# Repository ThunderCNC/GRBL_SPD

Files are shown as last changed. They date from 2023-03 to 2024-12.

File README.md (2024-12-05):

  

  <div align="center">
    <div style="display:inline-block; vertical-align: middle;">
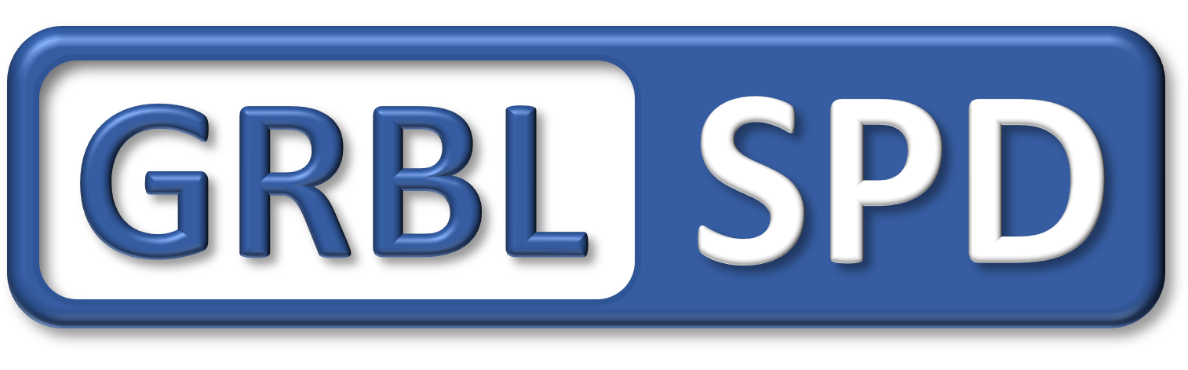
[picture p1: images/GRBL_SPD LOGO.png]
      
    </div>
  </div> 

  <div align="center" >
  <a href="https://www.ebay.ca/itm/226146198705" style="margin-right:10px">
    
  </a>
  <a href="https://www.facebook.com/ThunderCNC" style="margin-right:10px">
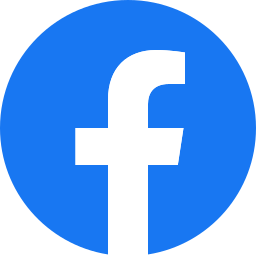
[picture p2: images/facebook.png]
Facebook
    
  </a>
  <a href="http://www.youtube.com/@Thunder116fd" style="margin-right:10px">
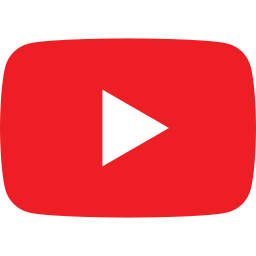
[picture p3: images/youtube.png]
Youtube
    
  </a>
  <a href="https://www.instagram.com/thunder_cnc/" style="margin-right:10px">
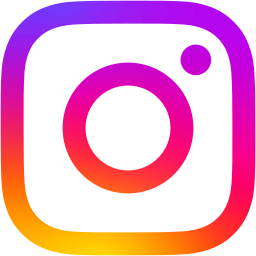
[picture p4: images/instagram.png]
Instagram
    
  </a>
  <a href="https://www.linkedin.com/in/jon-harrison-01428557" style="margin-right:10px">
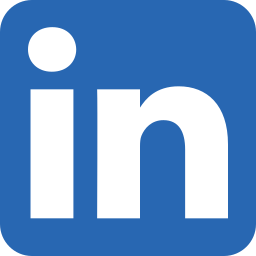
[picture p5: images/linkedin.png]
Linkedin
    
  </a>
  <a href="https://www.tindie.com/stores/gingertesla/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">
    
  </a>
  </div>
  </br>
  </br>
  <p align="center" >Developed to integrate software control of the Makita 701C for use with but not limited to the Arduino Uno board (Flashed with GRBL 1.1)
  </p>
  <h2>ABOUT THE GRBL_SPD</h2>
  <p>
    This project allows for automatic control of a standard Makita 701C router for CNC machines. GRBL_SPD lets you set the rpm for your bits in software such as Vectric and have it automatically set your router. This cicuit replaces the potentiometer in the router and has an accuracy of approximately between +/- 100 to 200 RPM. In most cases this deviation has no impact on the machining process. You no longer have to turn on the router before sending the file, GRBL_SPD will do it for you. There are inputs for manual control which overrides the RPM setting in the GRBL file being sent. 
  </p></br>
  <h2>VERSIONS</h2>
  <div>
    <h2>Version 3 -- Discontinued</h2>
    <p> Reason: ATtiny84 microcontroller reached end of life.</p>
    <a title="Go to v3 page" href="versions/Version_3.md">
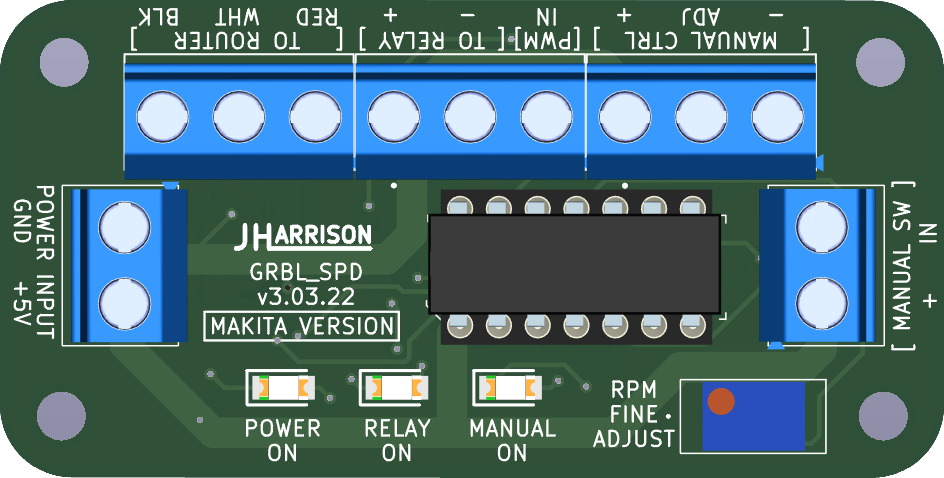
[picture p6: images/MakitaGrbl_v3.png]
      
    </a>
  </div></br>
  <div>
    <h2>Version 4 -- Available</h2>
    <p> Upgraded to ATtiny1624 microcontroller</p>
    <a title="Go to v4 page" href="versions/Version_4.md">
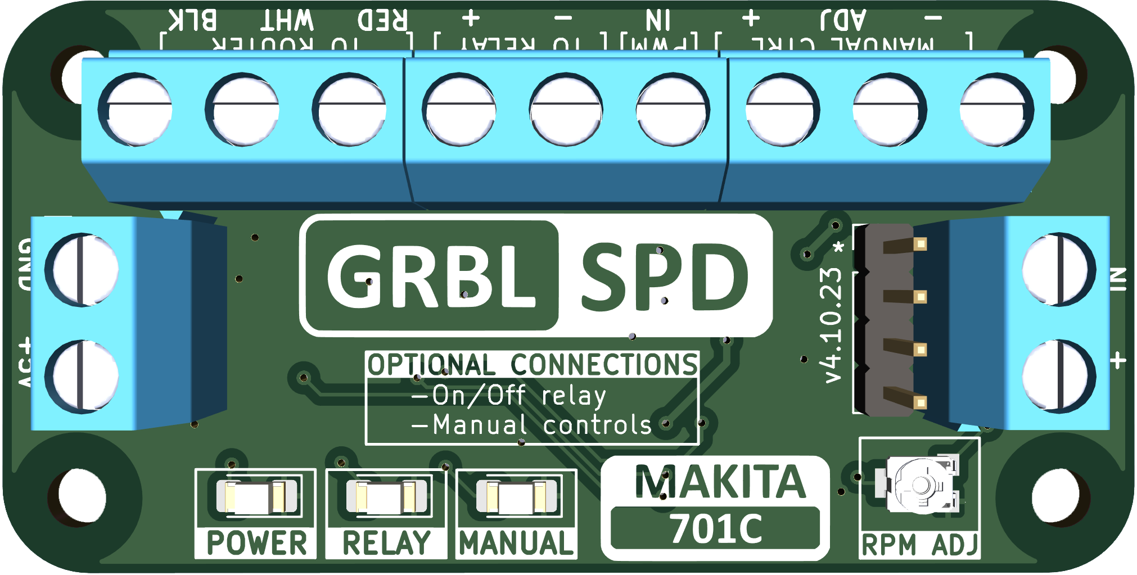
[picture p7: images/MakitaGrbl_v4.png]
      
    </a>
  </div></br>
  <!--<div>
    <h4>Version 5 -- Coming Soon</h4>
    <a title="Go to v5 page" href="versions/Version_5.md">
      <img height="150" src="images/MakitaGrbl_v5.png">
    </a>
  </div></br> -->

  <p> 
    <h2>Version 4 Features:</h2>
    <ul>
      <li>20MHz ATtiny1624 microcontroller</li>
      <li>10,000 to 30,000 RPM</li>
      <li>On/Off relay control</li>
      <li>Auto off when using manual override</li>
      <li>External manual controls</li>
    </ul>
  </p>

  <h2>Prerequisites:</h2>
    <ul>
      <li>+5v power and ground from CNC controller</li>
      <li>0-5v PWM signal from CNC controller</li>
      <li>1kHz PWM signal</li>
      <li>Sheilded cable between router and GRBL_SPD</li>
    </ul>

  <h2>Optional:</h2>
    <ul>
      <li>Connect relay for on/off function</li>
      <li>Potentiometer and switch for manual controls</li>
    </ul>

  <h3>Videos:</h3>
    <ul>
      <li>https://youtu.be/yv5z3KrGrSQ</li>
      <li>https://youtu.be/ecWwXNGC7Bc</li>
    </ul>

  <h4>Some users have tested with 240v Makita versions and have it functioning. I am not able to confirm this other than some video and testimony from those users. This board is designed for the Makita 701C so any other models will be experimenting at your own risk.</h4>

  Links to videos from Derek using the Makita 700C 240vac.
    <ul>
      <li>https://youtu.be/zJGl1yo-icU</li>
      <li>https://youtu.be/4u-4MBUV964</li>
    </ul>
  
  <h3><STRONG>WARNING!</STRONG> Voltages above 5v connected to this board will damage the microcontroller. If experimenting with controllers other than the standard Uno be sure to double check voltages and/or add protection to inputs. Zener and resistor for example.</h3>
  <h3>Possible high voltage setup:</h3>
  <div>
  <a href="images/higherVoltage2.png">
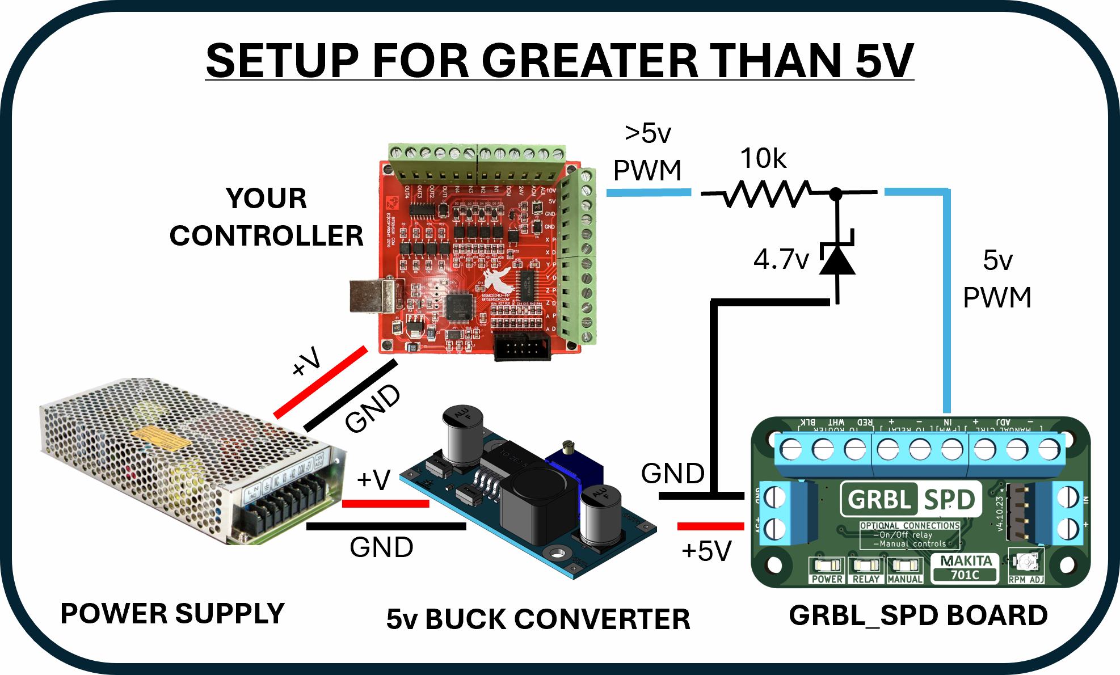
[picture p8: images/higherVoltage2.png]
    
  </a>
  </div>

<p align="right">(<a href="#readme-top">back to top</a>)</p>

  <h2>Controller Settings</h2>
 
 ```C
GRBL 1.1  config.h

 #define VARIABLE_SPINDLE // Default enabled. Comment to disable.

 #define SPINDLE_PWM_MIN_VALUE 2 // Default disabled. Uncomment to enable. Must be greater than zero. Integer (1-255).
 ```

 ```
GRBL settings

$30=30000
$31=10000
$32=0
 ```

 Depending on your sending software and controller setup there may be a setting for PWM frequency which should be 1kHz. There may also be settings for PWM voltage 0-5v or 0-10v so make sure it's set for 0-5v. A few different senders also have their own settings for min and max RPM so they should match the grbl settings. If your software/controller has mapping than you may need to set PWM accordingly so that 0% is off, 1 or 2% is min and 100% is max. 

 <h2> Connections</h2>
     <ul>
      <li>Power Input --> [+5v] and [GND] from controller 5v and ground</li>
      <li>PWM --> [PWM] 0-5v PWM from controller</li>
      <li>Router --> [RED] / [WHT] / [BLK] from router</li>
      <li>Relay --> [-] and [+] to relay coil</li>
      <li>Manual SW --> [IN] and [+] to switch</li>
      <li>Manual CTRL --> [-] / [ADJ] / [-] to potentiometer</li>
    </ul>
<div>
<a href="images/ConnectionDiagram_v4.png">
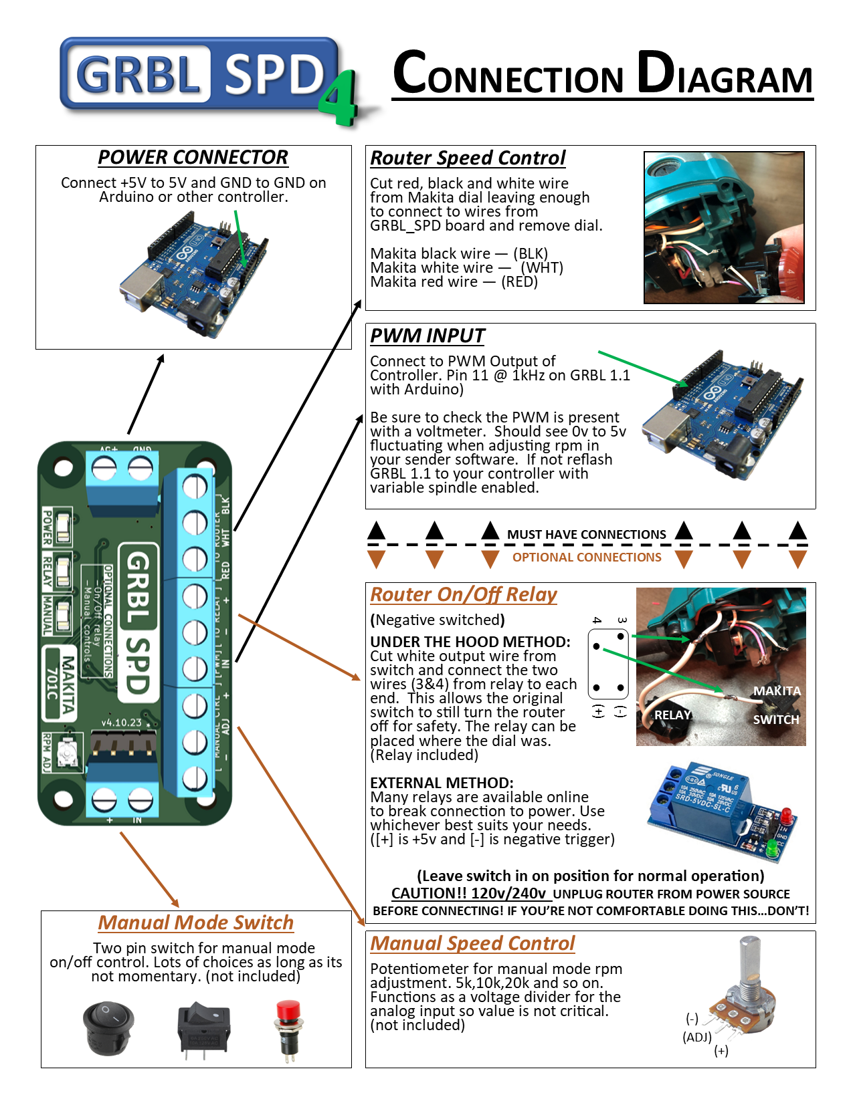
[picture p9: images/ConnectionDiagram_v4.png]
  
</a>
</div>
</br>
</br>
</br>

<p align="right">(<a href="#readme-top">back to top</a>)</p>

<h1> Before You Begin </h1>
First thing to do is to check whether your controller is setup for the PWM signal.  Make sure GRBL 1.1 is flashed to your controller.

1. If it is then with your machine turned on and using your favorite sender software, measure the voltage on the PWM (Arduino pin 11) while you adjust the RPM in the software.  It should read voltages between 0v and 5v and change up and down with the software.  If it does than you’re good to go.
2. If it doesn’t than you will need to re-flash your controller.  There are many resources on how to do this on the web.

<h3>Flashing GRBL</h3>

1. Make note of all your machine settings on your controller.
2. Download GRBL 1.1 latest version.
3. Uncomment enable variable spindle in config.h.
4. Flash to your controller.
5. If machine settings are gone enter them from notes.

<h3>Items Not Provided</h3>

1. Wire long enough to run from the GRBL_SPD to the router (5 wires) and from the GRBL_SPD to the optional manual controls (5 wires).  In the range of 22 gauge as all these connections are low voltage and low current. Shielded cables are recommended to protection from interference.
2. Standoffs or other method to mount GRBL_SPD inside control case.  Old computer motherboard standoffs, PCB adhesive standoffs (Amazon) or however you see fit.
3. Soldering iron or connectors to make the connections inside the router and to the optional switch with potentiometer.
4. Electrical tape or heat shrink.
5. Small zip ties if necessary to keep things tidy.

<h3>The Router </h3>
Start by removing the router and remove the four screws holding the cap.  Once open, run the wiring through the cover before making any connections.  Now locate the red/white/black wires from the speed dial.  Cut these wires and remove the Makita dial making sure there is enough wire left to make the connections.  Connect the Makita red/white/black to GRBL_SPD red/white/black (refer to connection diagram). Locate the white wire from the Makita switch if you are connecting the internal optional relay.  Cut the white wire leaving enough length to make connections to both ends.  Connect high voltage wires from relay to both ends of the cut white wire (refer to connection diagram).  Connect low voltage wires to remaining connections on the relay(refer to connection diagram).  The relay can be placed in the cavity on the opposite side of the main power connector or where the speed dial used to be.  Screw the top of the router back on making sure not to pinch any wires and mount router back onto CNC.

<div>
<a href="images/IMG_5855.JPG">
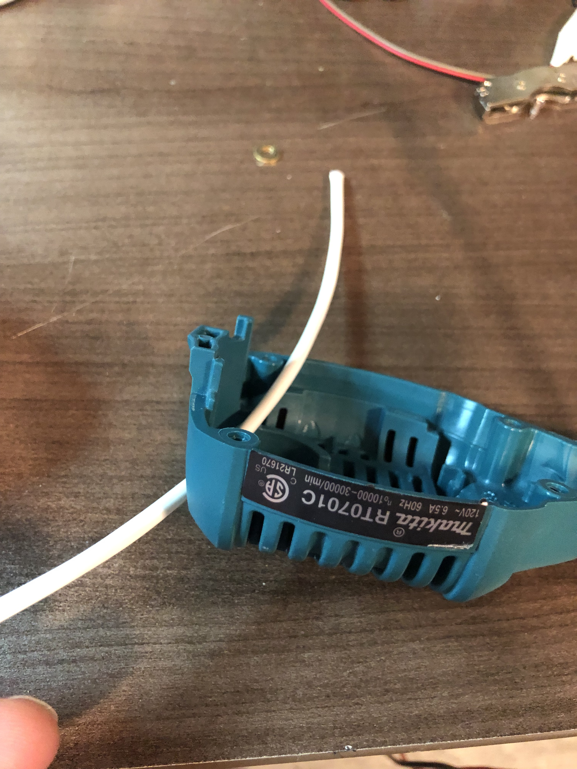
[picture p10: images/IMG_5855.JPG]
  
</a>
<a href="images/IMG_5860.JPG">
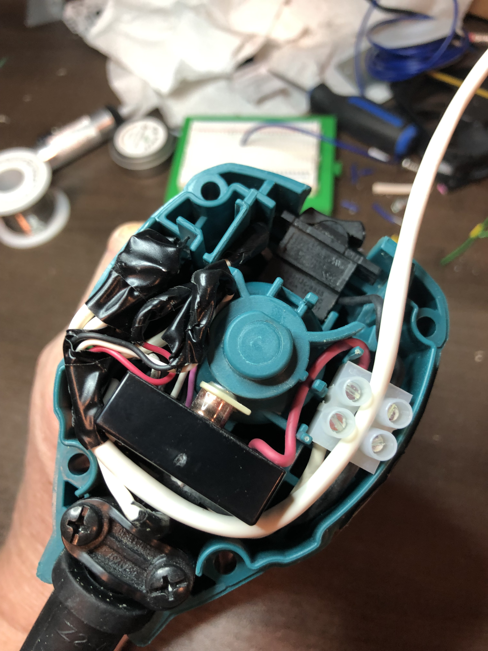
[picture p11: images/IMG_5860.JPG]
  
</a>
<a href="images/Picture1.png">
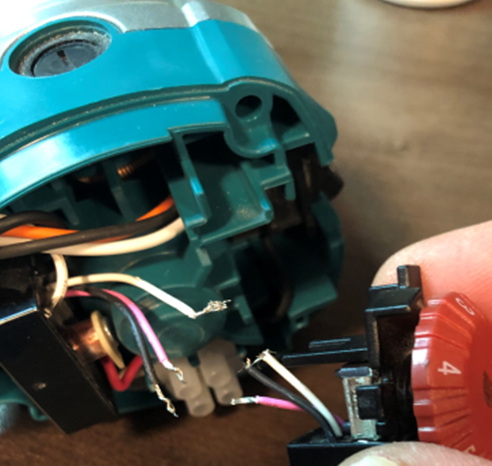
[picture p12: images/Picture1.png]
  
</a>
<a href="images/Picture2.png">
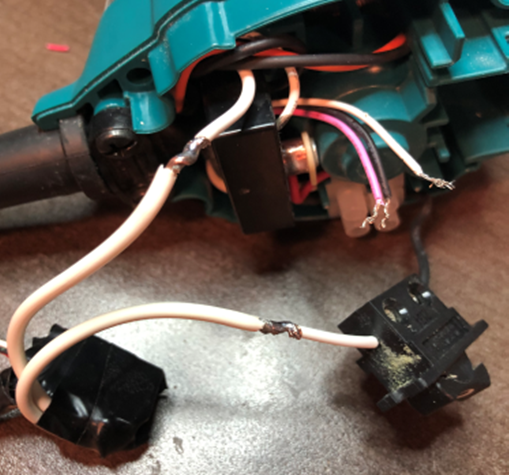
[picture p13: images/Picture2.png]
  
</a>
<a href="images/IMG_5862.JPG">
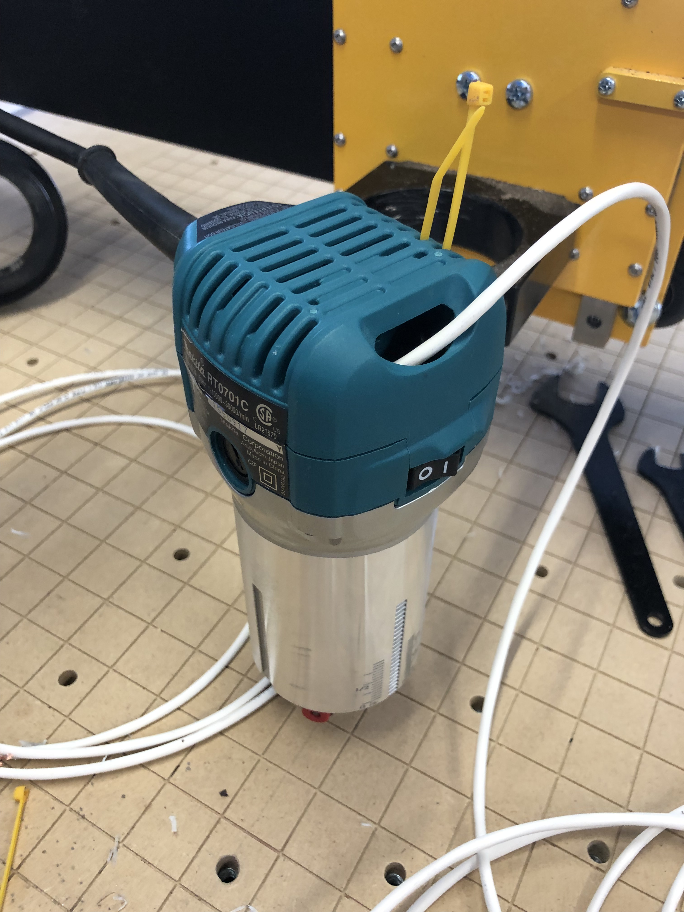
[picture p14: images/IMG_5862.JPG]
  
</a>
</div>
<p align="right">(<a href="#readme-top">back to top</a>)</p>

<h3>Optional Manual Control<h3>
If you have downloaded and printed the stl file provided here then start by running the wires through the printed hole at the back.  If your wires are going to go downward from the enclosure then start by connecting the wiring to the potentiometer (refer to connection diagram).  Mount the potentiometer and the switch into the 3D printed enclosure. Connect the remaining two wires to the switch.  
This enclosure is made to snap onto the Millright Mega V leg.  If you're not using this enclosure then do as you need and make the same connections as per your mount.

<div>
<a href="images/IMG_5917.JPG">
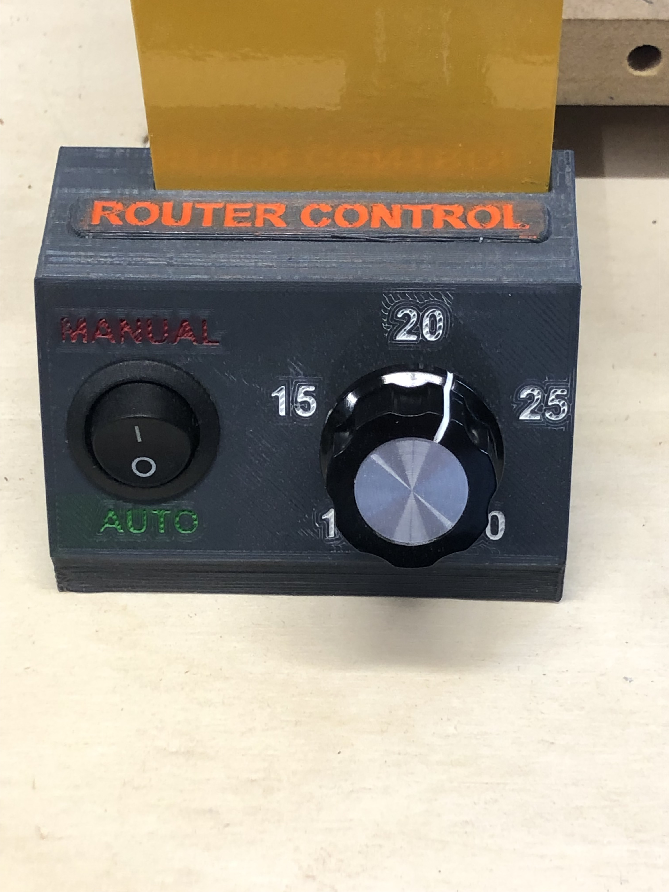
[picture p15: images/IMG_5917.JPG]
  
</a>
<a href="images/IMG_5918.JPG">
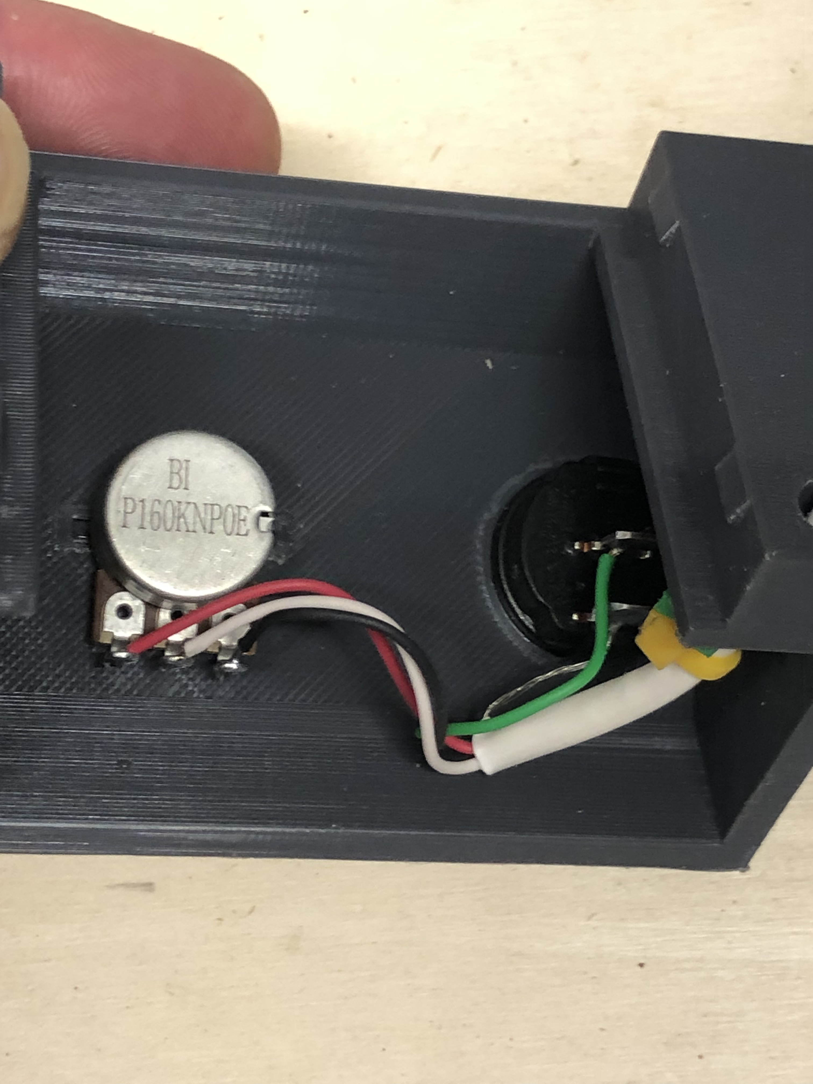
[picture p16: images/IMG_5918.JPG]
  
</a>
</div>

<h3>The Mount:</h3>

The STL files for this mount and the filler piece are located in the stl folder.

<div>
<a href="images/ControlPanel2.JPG">
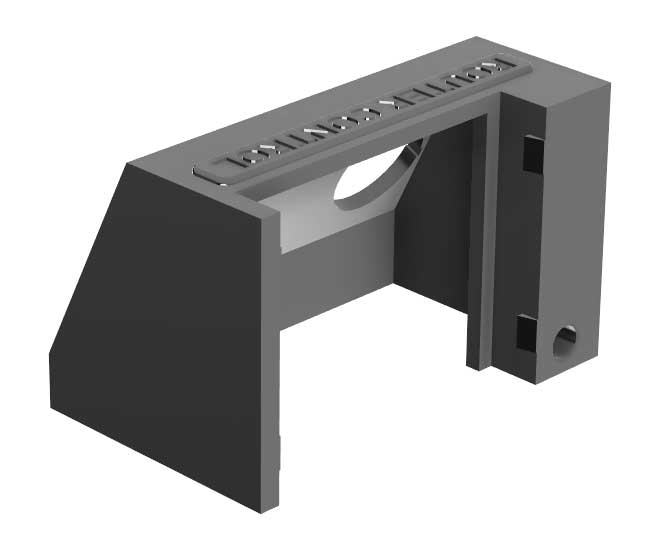
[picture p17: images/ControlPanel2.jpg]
  
</a>
<a href="stl/Filler3.JPG">
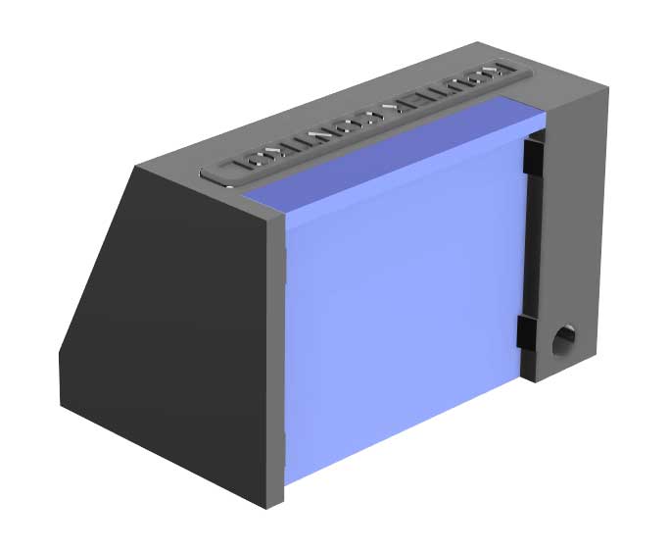
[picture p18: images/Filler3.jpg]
  
</a>
</div>

<h3> GRBL_SPD Connections:</h3>
Run the wire from the router to the control box through the drag chains if equipped. Run the wires from the manual controls if installed.  Make the router and manual control connections to the GRBL_SPD board (refer to connection diagram). Connect the PWM wire to the GRBL controller. Connect the 5v power and ground to the GRBL controller.  Take a moment to check all connections.

<h3>CHECKS:</h3>

1. Turn on you CNC with the computer connected and the sender software running.  Check that the POWER ON led is on.
2. Turn the manual control switch on if you have it. The spindle should be running at what the dial is indicating. Check that the RELAY ON led and the MANUAL ON led are on.  Turn the knob from left (10000 rpm) to right (30000 rpm).  If the RPM is reacting opposite to the dial then the potentiometer wires have been connected incorrectly. Reverse the (+) and (-) wires at the GRBL_SPD board.
3. In your sender software be sure to set $30 to 30000 and $31 to 10000. Also make sure if there is a configuration section in the software, be sure to check that the min and max rpm are set the same. You may need to restart the software after changes are made.
4. With manual turned off, start the spindle with the software.  Adjust to different RPM to ensure it’s functioning.  If it’s not then check your connections and/or ensure that the variable spindle option is enabled in GRBL with a voltmeter.
5. If all is well and you have the manual controls, turn the spindle on with the software set at 15000 rpm.  Set the manual dial to 30000 rpm and turn on the switch.  Rpm should not have changed.  Slowly turn the dial down towards 15000 rpm and when it is close, the manual control will take over.  If the switch is turned off it will revert back to the software setting.  If you’re in the middle of a path and want to override the software speed, leave the switch on until complete. The router will turn off when the path is complete.
6. Test your M3, M5, S##### commands.

Now you can set your speeds for each bit in your cad software of choice and your router will automatically be set to your required speed.  When your path is finished the router will turn off when complete.

<h3>NOTES:</h3>

The GRBL_SPD board you receive has been tested and calibrated with a Makita 701C router. There could be slight differences in routers but the variance in RPM shouldn’t be too drastic. If you have a handheld tachometer then you can test and adjust the RPM with the trimmer resister if necessary.  In your sender software of choice turn on the router and set it for 20000 rpm.  Take a reading with the tachometer and adjust the trimmer until it’s as close to 20000 as possible.

That’s it, congratulations you’re done!

Any questions drop me an email at jharrison116@hotmail.com or message me through the social links at the top of this page.

<p align="right">(<a href="#readme-top">back to top</a>)</p>

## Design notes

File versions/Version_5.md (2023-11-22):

<!DOCTYPE html>
<html lang="en">
<head>

</head>
<body> 
  <h1 align="center">GRBL_SPD v5 (Makita 701c)</h1>
  <div align="center">    
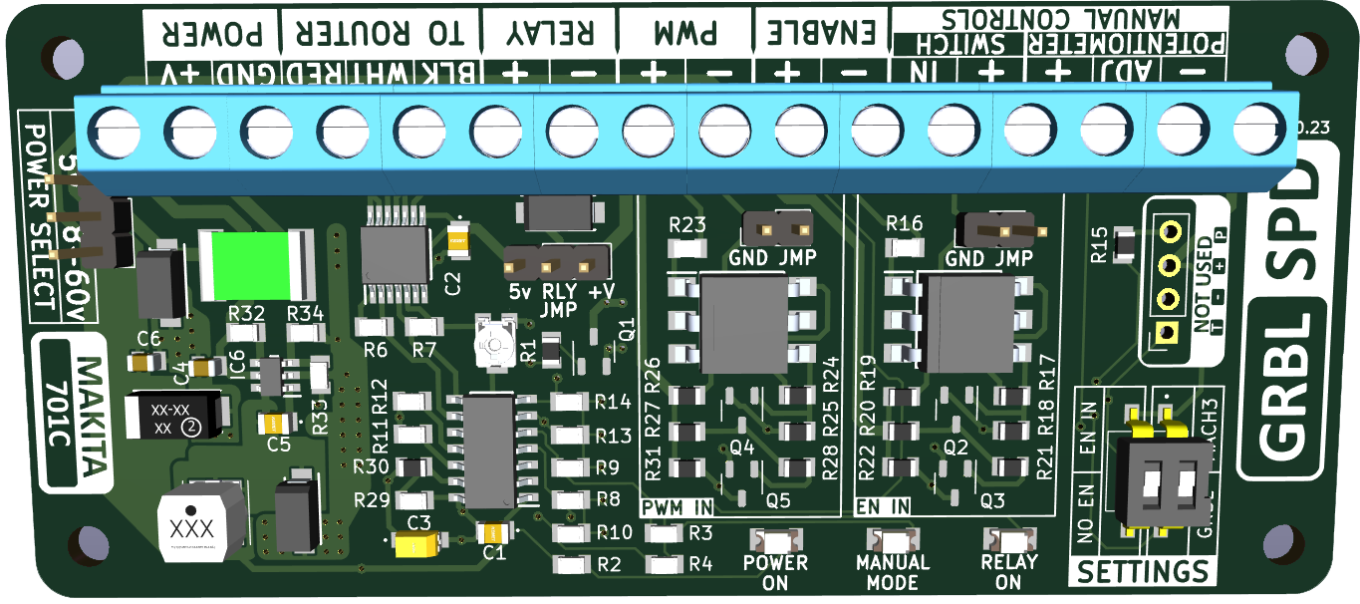
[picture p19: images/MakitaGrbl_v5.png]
        
  </div></br>
  <h1 align="center">COMING SOON!</h1>
</body>

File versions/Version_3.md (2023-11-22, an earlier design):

<!DOCTYPE html>
<html lang="en">
<head>

</head>
<body> 
  <h1 align="center">GRBL_SPD v3 (Makita 701c)</h1>
  <div align="center">    
        
  </div></br>

  <div align="center">
  <p >Link to purchase kits</p>
  <a href="https://www.tindie.com/stores/gingertesla/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">
    
  </a>
  </div>

  <p> 
    <h2>Features for Makita 701C:</h2>
    <ul>
      <li>10,000 to 30,000 RPM</li>
      <li>On/Off control</li>
      <li>External manual controls</li>
    </ul>
  </p>

  <h2>CONNECTIONS</h2>
   <p><b><i>OPTIONAL CONNECTIONS:</i></b></br>  The three connections to control the RPM of the router and the PWM are neccessary. The potentiometer, switch and relay are not neccessary for function. It's up to you what you connect. 
  </p>
  <p><b><i>CONTROLLER TO GRBL_SPD:</i></b></br>  Connections from the controller to the GRBL_SPD include power (5v), ground, and the PWM (0-5v) signal. Since both on/off and rpm are durived from the PWM pin, you must ensure in your post processor that S0 is included at the end of the file. Some grbl senders will automatically send S0 when M5 is sent, some will not so it's better to add it. Power and ground from the controller are self explanitory when using Arduino as they are clearly marked.
  </p>
  
  <p><b><i>GRBL_SPD TO ROUTER:</i><b></br>  There are five connections inside the router. Three are to the the wires left when the router speed dial is removed and the other to connect to the relay. The cable/cables used for these connections should be shielded to help eliminate EMF. The relay breaks the power connection to the router and by leaving the connection to the factory switch makes for a fail safe. There is plenty of room inside the router housing for the relay to make things neat but it can be anywhere along the mains line.
  </p>
  
  <p><b><i>MANUAL CONTROL TO GRBL_SPD:</i><b></br> This feature has five connections as well. Three connect to an external potentiometer and two connect to a switch. At any point with the power on to the controller the switch will activate the router. When a file is being sent and a cut path is in progress, if needed you can turn on the switch to override the set RPM. To ensure there is no sudden drop or rise in RPM it will not override until the manual dial is within approx 2% of the set RPM. 
  </p>
    
  <h2>INSTALLATION</h2>
  <figure>
      <figcaption>Installation Diagrams:</figcaption>
      <ul>
        <li><a href="https://github.com/ThunderCNC/GRBL_SPD/blob/main/installation/ConnectionDiagram.pdf">Connection Diagram (Arduino Uno format)</a></li>
      </ul>
  </figure>
  <figure>
      <figcaption>STL files for manual control:</figcaption>
      <ul>
        <li><a href="https://github.com/ThunderCNC/GRBL_SPD/blob/main/stl/ManualMount.stl">Manual Control Mount (Millright MegaV)</a></li>
        <li><a href="https://github.com/ThunderCNC/GRBL_SPD/blob/main/stl/FillerMount.stl">Manuall Control Filler (For non-MegaV CNCs)</a></li>
      </ul>
  </figure>
  <p><b><i>CONTROLLER TO GRBL_SPD:</i></b>
    
  </p>
</body>
</html>

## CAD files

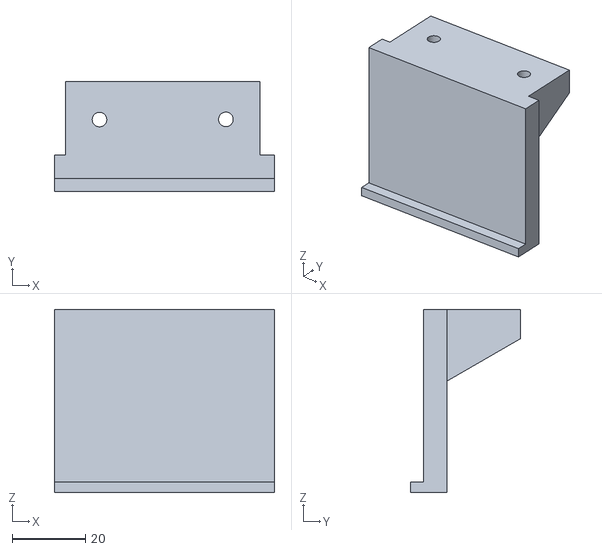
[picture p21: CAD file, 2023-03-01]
stl/FillerMount.stl
60.0 x 30.0 x 50.0

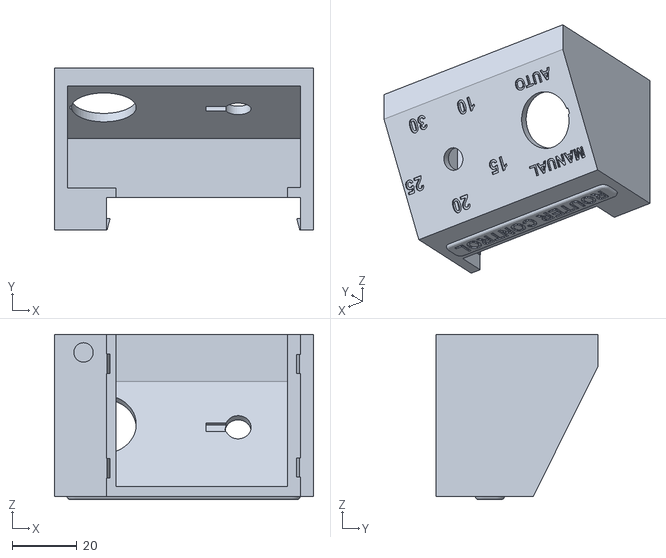
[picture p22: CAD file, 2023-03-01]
stl/ManualMount.stl
80.0 x 49.9 x 51.0

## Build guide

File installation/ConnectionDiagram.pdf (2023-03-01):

## Router On/Off Relay

Cut white output wire from switch and connect the two wires (3&4) from relay to each end. This allows the original switch to still turn the router off for safety. The relay can be placed where the dial was. (Leave switch on for normal operation)
CAUTION!! 120v/240v
UNPLUG FROM ROUTER FROM POWER SOURCE BEFORE CONNECTING!

## PWM INPUT

Connect to PWM Output
(pin 11 on GRBL 1.1)
Be sure to check the PWM is present with a voltmeter. Should see 0v to 5v fluctuating when adjusting rpm in your sender software. If not reflash GRBL 1.1 to your controller with variable spindle enabled.

## Router Speed Control

Cut red, black and white wire from Makita dial leaving enough to connect to wires from GRBL_SPD board and remove dial.

Makita black wire — (BLK)
Makita white wire — (WHT)
Makita red wire — (RED)

## Manual Speed Control

(OPTIONAL)
Potentiometer for manual mode rpm adjustment.

## Manual Mode Switch

(OPTIONAL)
Two pin rocker switch for manual mode on/off control. Non-polarized connection so (+) and (IN) can be connected to either pin.

## POWER CONNECTOR

Connect +5V to 5V and GND to GND on Arduino.

3

4

# GRBL_SPD CONNECTION DIAGRAM

(+)

## (ADJ)

(-)

## OPTIONAL MANUAL CONTROL Both must be installed for this

feature to work.

(-)
(+)

## RELAY

## MAKITA SWITCH

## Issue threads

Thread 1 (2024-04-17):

Can I connect this to a Foxalien Masuter Pro?

brandoncordell, 2024-04-17:
I opened up my Master Pro controller today and saw that I have an empty 3-pin PWM socket. If I supply GRBLSPD with 5.5v and connect this up like the instructions layout, will it work?

ThunderCNC, 2024-04-17:
Hi Brandon,
I was trying to find a circuit diagram for your cnc but could not find one. If the pwm on your controller is 5v max and it has a 5v power rail to supply the GRBL_SPD it should work.

brandoncordell, 2024-04-17:
Thanks! If the PWM is more than 5v, would it be safe to add resistors or a buck converter inline to get it down to 5v? I'll pull out the multimeter in the morning. Thanks so much!

ThunderCNC, 2024-04-17:
No worries. Anytime. 5.5v is max for the microcontroller. I would be hesitant on running that voltage. I’ve seen on other controllers the pwm being labeled ttl. If so it should be 5v max. If need be a resistor voltage divider would work with little to no error. Buck would probably distort the signal too much. Also if your setup allows the pwm should be set for 1kHz if possible.
In the version 5 I used optocouplers to accept multiple voltage levels and a bunch of filtering but they won’t be available for a couple months. Version 4 will be available the end of the month but it is the same layout as V3, just faster.
Cheers!

brandoncordell, 2024-04-19:
Pulled out the multimeter today after getting some free time and it looks like the available power rails are 12v and 48v. The PWM is 12v as well. Looks like a 4.8k ohm and 6.8k ohm resistors will get me down to 5v. Hopefully that will work out.

> Buck would probably distort the signal too much.

Was this in regards to just the PWM? Can I use one for just powering the microcontroller?

ThunderCNC, 2024-04-19:
Yes I was referring to the pwm. A buck on the either of the two power rails to power it would be fine but 12v would be preferred. Resistor values you stated look good. Another option would be to use a mosfet level shifter for the pwm.

Closed 2024-12-09.

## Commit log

2024-12-05 couple errors
    fixed a couple errors
2024-12-09 stl file size change
2024-12-09 corrected stl image
2024-12-09 playing with stl link
